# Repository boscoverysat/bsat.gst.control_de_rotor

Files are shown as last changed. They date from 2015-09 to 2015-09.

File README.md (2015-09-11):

# Control de Rotor

## Resumen

Este repositorio contiene la adaptación de la electrónica de control empleada para el rotor de antena basado en el proyecto **[SatNOGS](https://satnogs.org/)**

## Autoría y Licencia

- Autor: **Dailos Rafael Díaz Lara** ( ddialar@gmail.com )
- Fecha: **11/09/2015**
- Versión: **1.0.0**
- Licencia: Creaive Commons 4.0 logo (http://creativecommons.org/licenses/by-nc-sa/4.0/)

## Requisitos previos

- Tener instalado el entorno de desarrollo para Arduino.
- Tener instalado el software Eagle PCB 6.5.0+.

## Procedimiento

Este repositorio contiene la adaptación de la electrónica de control empleada para el rotor de antena basado en el proyecto **[SatNOGS](https://satnogs.org/)** ([Repositorio de origen](https://github.com/satnogs/satnogs-rotator-controller)).

Esta adaptación se ha realizado para utilizar una placa **Ardino Duemilanove** en lugar de la placa *Ardiono Pro Micro*
empleada originalmente.

Para poder llevar a cabo esta adaptación, además de reorganizar la electrónica en torno a los pines del Arduino a emplear,
ha sido necesario reconfigurar los pines dentro del código fuente que será cargado en el microcontrolador.

La organización de directorios de este repositorio es la siguiente:

### [arduino](arduino/)

Contiene el archivo de código fuente que debe cargarse en el microcontrolador.

Para que este script funcione, es necesario incorporar en nuestro entorno de desarrollo, una librería adicional
que no suele venir con la instalación estándar. Dicha librería es **AccelStepper.h** y puede ser localizada
en el siguiente [enlace](https://github.com/adafruit/AccelStepper).

Para concluir, hay que indicar que la única diferencia entre el script original y el empleado en este repositorio, reside en que se ha modificado la numeración de los pines empleados para el control de los motores paso a paso, así como para la detección de la posición HOME de los ejes de Elevación y Azimuth.

En el código fuente que contiene el directorio, se ha mantenido la definición original de pines (comentada para que no tenga efecto en el código), con el propósito que sirva de referencia en futuras investigaciones.

### [img](img/)

Contiene una imagen del conexionado de la placa PCB.

### [pcb](pcb/)

Contiene el proyecto de placa de circuito impreso, realizado con el software **Eagle 6.5.0**.

### [pdf](pdf/)

Contiene el esquema electrónico y el diagrama PCB listos para ser impresos.

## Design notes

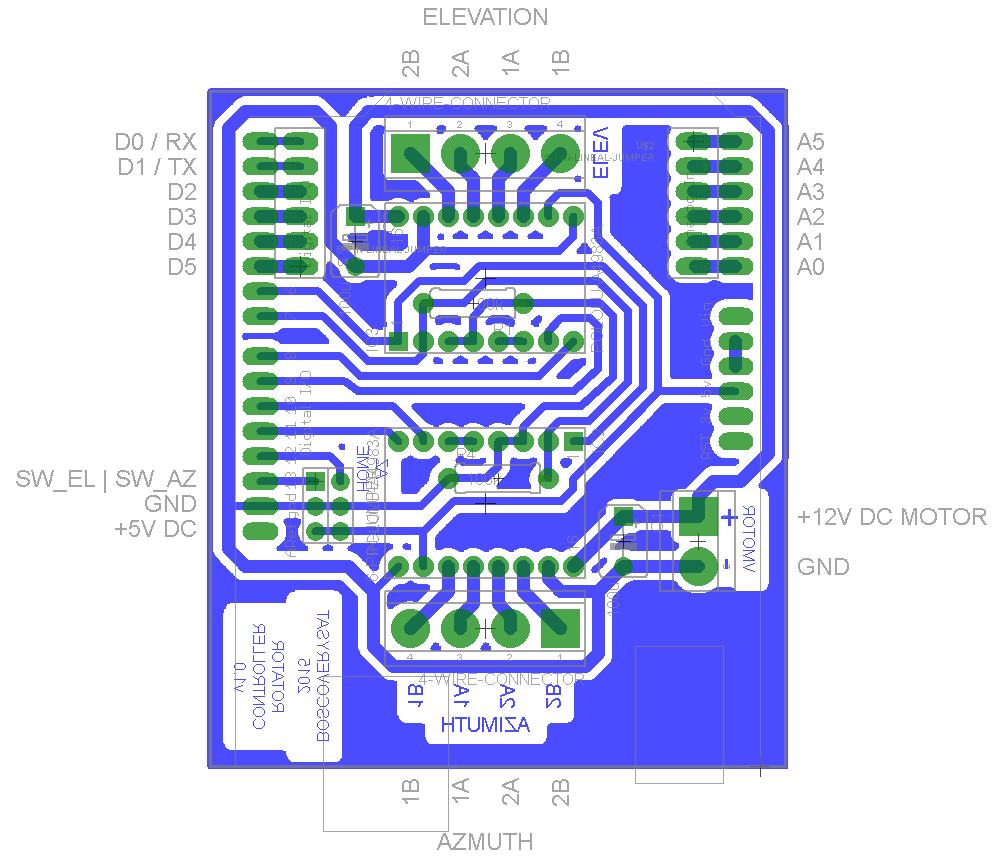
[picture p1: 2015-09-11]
img/Rotator Controller - Arduino Duemilanove.png

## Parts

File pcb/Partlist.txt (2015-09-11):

Partlist

Exported from SatNOGSBoard UNO.brd at 11/09/2015 22:43:30

EAGLE Version 6.5.0 Copyright (c) 1988-2013 CadSoft

Assembly variant: 

Part     Value               Package             Library      Position (inch)       Orientation

C1       100u                B45181B             resistor     (1.85 1.3)            R270
C2       100u                B45181B             resistor     (0.78 2.5)            R270
IC1      ARDUINOUNO          ARDUINO             boscoverysat (2.4 0.4)             R90
IC2      POLOLU-A4983A       POLOLU-A4983        boscoverysat (1.3 1.45)            R270
IC3      POLOLU-A4983A       POLOLU-A4983        boscoverysat (1.3 2.35)            R90
MOTOR_1  4-WIRE-CONNECTOR    4-WIRE-CONNECTOR    boscoverysat (1.3 0.95)            R180
MOTOR_2  4-WIRE-CONNECTOR    4-WIRE-CONNECTOR    boscoverysat (1.3 2.85)            R0
R1       100k                0309/10             resistor     (1.25 2.25)           R180
R4       100k                0309/10             resistor     (1.35 1.55)           R0
SW       6-PIN-JUMPER        6-PIN-JUMPER        boscoverysat (0.62 1.54)           R270
U$1      6-PIN-LINEAL-JUMPER 6-PIN-LINEAR-JUMPER boscoverysat (0.56 2.4)            R0
U$2      6-PIN-LINEAL-JUMPER 6-PIN-LINEAR-JUMPER boscoverysat (2.13 2.9)            R180
VMOTOR   2-WIRE-CONNECTOR    2-WIRE-CONNECTOR    boscoverysat (2.15 1.3)            R270

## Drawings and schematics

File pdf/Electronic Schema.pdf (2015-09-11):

A

A

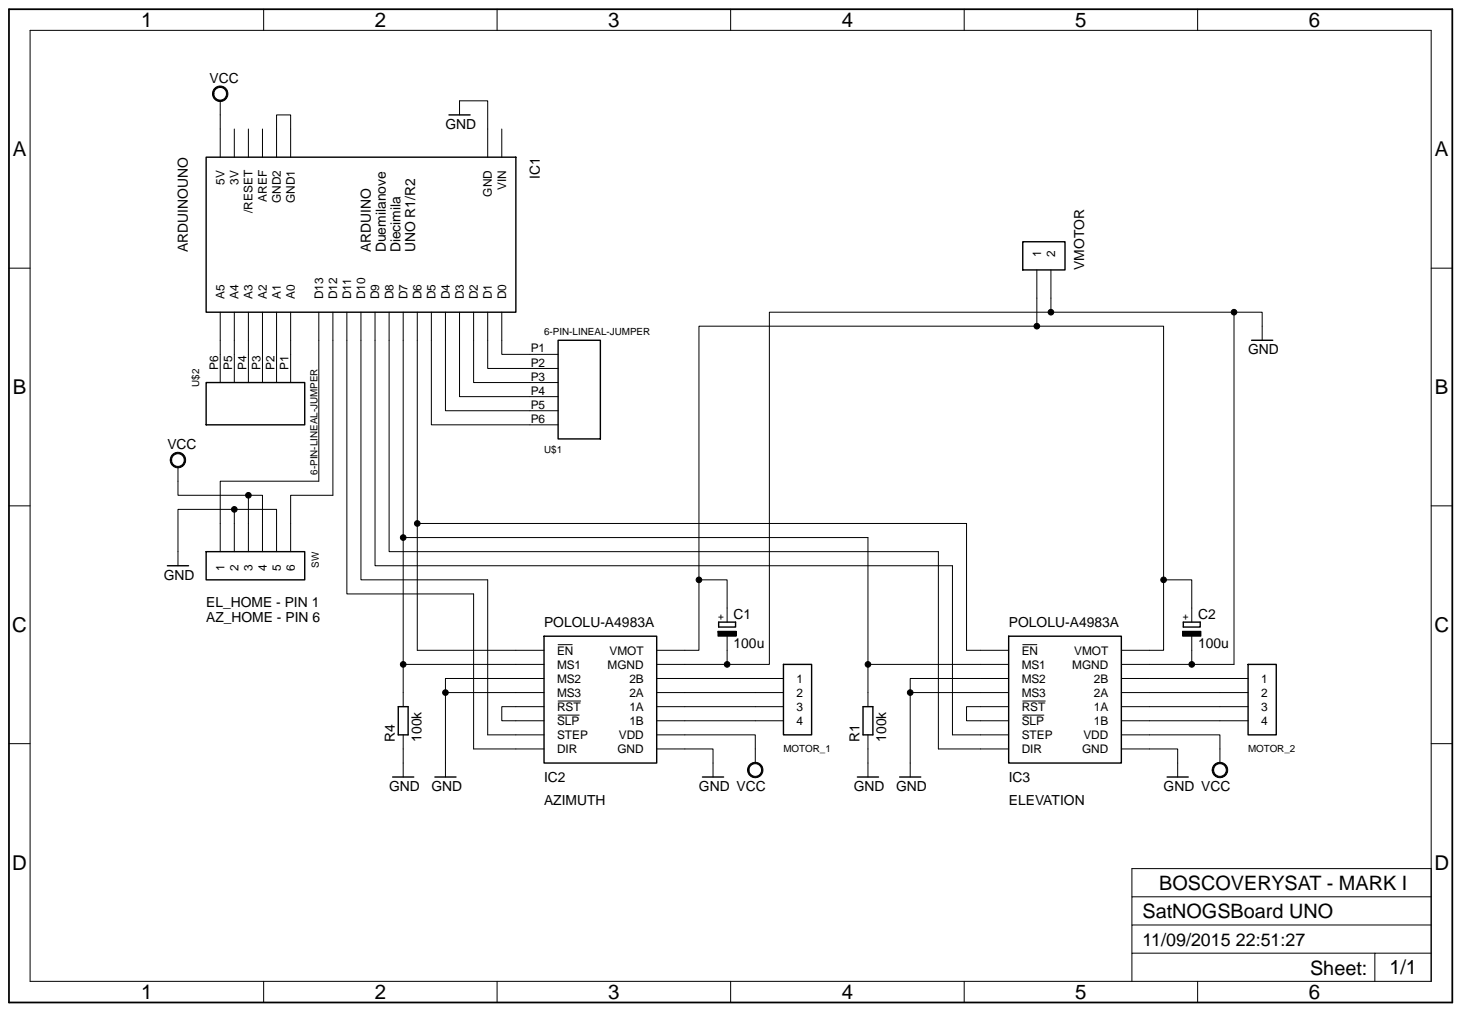
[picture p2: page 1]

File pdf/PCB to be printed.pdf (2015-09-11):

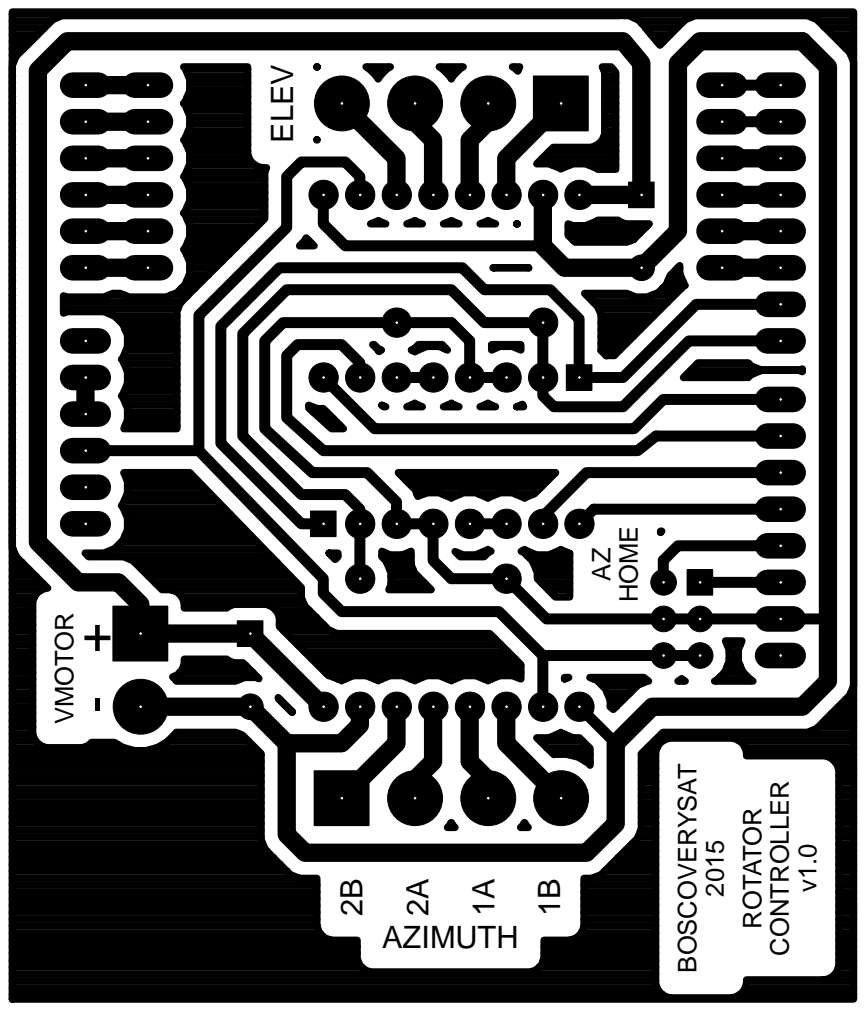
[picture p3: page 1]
ROTATOR; CONTROLLER; BOSCOVERYSAT; VMOTOR; AZIMUTH; HOME; ELEV

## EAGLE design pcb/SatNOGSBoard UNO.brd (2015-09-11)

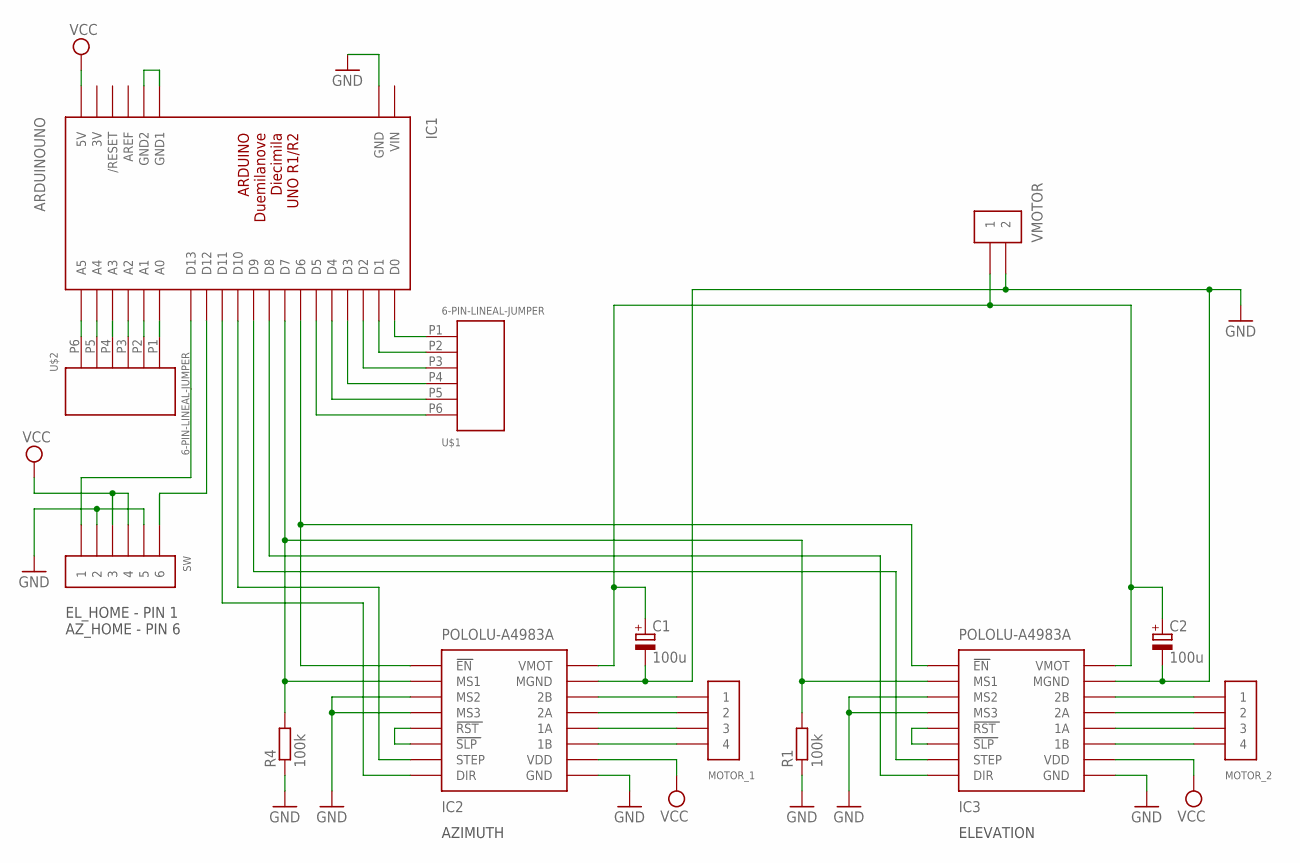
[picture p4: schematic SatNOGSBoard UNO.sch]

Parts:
C1, C2: 100u; B45181B
IC1: ARDUINOUNO; ARDUINO
IC2, IC3: POLOLU-A4983A; POLOLU-A4983
MOTOR_1, MOTOR_2: 4-WIRE-CONNECTOR
R1, R4: 100k; 0309/10
SW: 6-PIN-JUMPER
U$1, U$2: 6-PIN-LINEAL-JUMPER; 6-PIN-LINEAR-JUMPER
VMOTOR: 2-WIRE-CONNECTOR

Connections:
3V: IC1.3V
GND: C1.-, C2.-, IC1.GND, IC2.P$3 (MS2), IC2.P$4 (MS3), IC2.P$9 (GND), IC2.P$15 (MGND), IC3.P$3 (MS2), IC3.P$4 (MS3), IC3.P$9 (GND), IC3.P$15 (MGND), R1.1, R4.1, SW.P$2 (2), SW.P$5 (5), VMOTOR.P$2 (2)
unnamed: IC1.D6, IC2.P$1 (EN), IC3.P$1 (EN)
unnamed: IC1.D7, IC2.P$2 (MS1), IC3.P$2 (MS1), R1.2, R4.2
unnamed: IC3.P$5 (RST), IC3.P$6 (SLP)
unnamed: IC1.D9, IC3.P$7 (STEP)
unnamed: IC1.D8, IC3.P$8 (DIR)
unnamed: IC1.D0, U$1.P1
unnamed: IC1.D1, U$1.P2
unnamed: IC1.D11, IC2.P$8 (DIR)
unnamed: IC1.D12, SW.P$6 (6)
unnamed: IC3.P$14 (2B), MOTOR_2.P$1 (1)
unnamed: IC3.P$13 (2A), MOTOR_2.P$2 (2)
unnamed: IC3.P$12 (1A), MOTOR_2.P$3 (3)
unnamed: IC3.P$11 (1B), MOTOR_2.P$4 (4)
unnamed: IC2.P$5 (RST), IC2.P$6 (SLP)
unnamed: IC1.D2, U$1.P3
unnamed: IC1.D13, SW.P$1 (1)
unnamed: IC1.D3, U$1.P4
unnamed: IC1.D10, IC2.P$7 (STEP)
unnamed: IC2.P$14 (2B), MOTOR_1.P$1 (1)
unnamed: IC2.P$13 (2A), MOTOR_1.P$2 (2)
unnamed: IC2.P$12 (1A), MOTOR_1.P$3 (3)
unnamed: IC2.P$11 (1B), MOTOR_1.P$4 (4)
unnamed: IC1.D4, U$1.P5
unnamed: IC1.D5, U$1.P6
unnamed: IC1.A0, U$2.P1
unnamed: C1.+, C2.+, IC2.P$16 (VMOT), IC3.P$16 (VMOT), VMOTOR.P$1 (1)
unnamed: IC1.A1, U$2.P2
unnamed: IC1.A2, U$2.P3
unnamed: IC1.A3, U$2.P4
unnamed: IC1.A4, U$2.P5
unnamed: IC1.A5, U$2.P6
unnamed: IC1.GND1, IC1.GND2
VCC: IC1.5V, IC2.P$10 (VDD), IC3.P$10 (VDD), SW.P$3 (3), SW.P$4 (4)
VIN: IC1.VIN

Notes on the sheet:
ELEVATION
AZIMUTH
EL_HOME - PIN 1 AZ_HOME - PIN 6

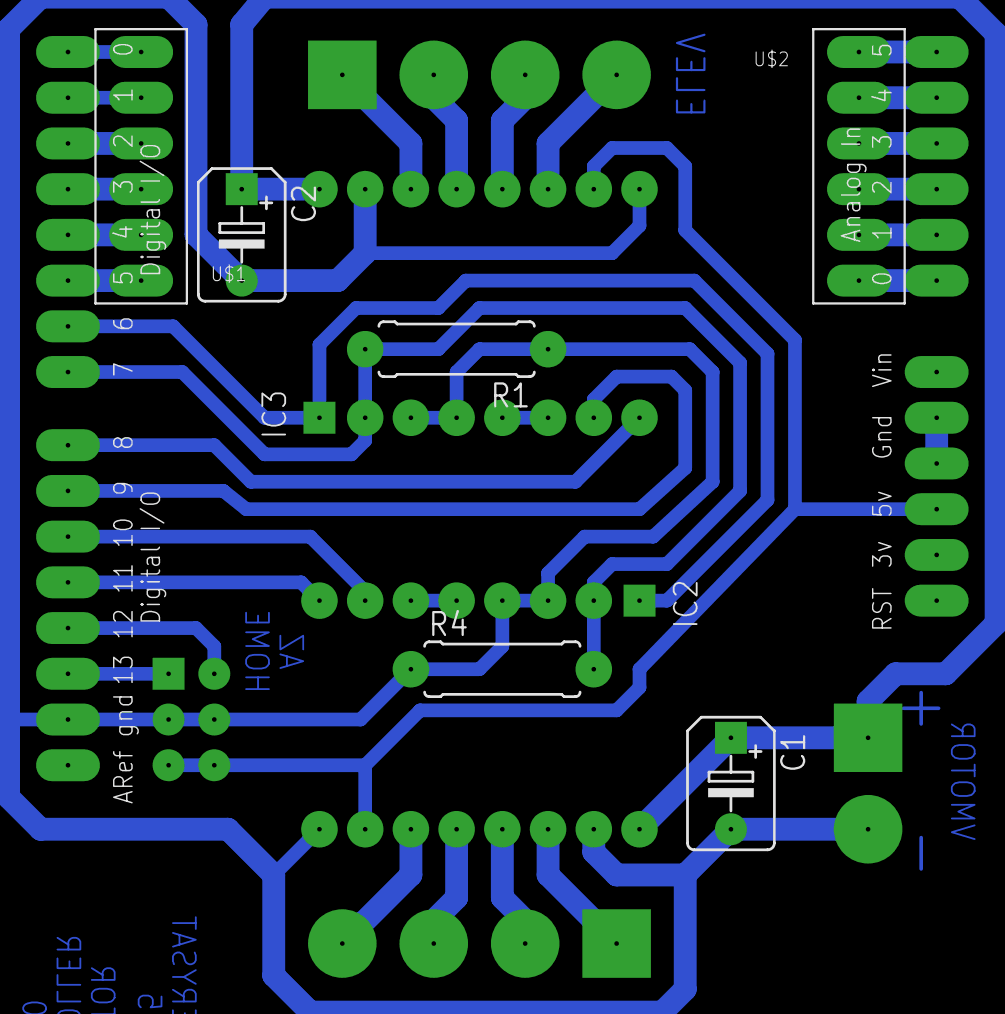
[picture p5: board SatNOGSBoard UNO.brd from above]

Board: 2 copper layers, 13 parts (0 on the bottom side), 34 nets.

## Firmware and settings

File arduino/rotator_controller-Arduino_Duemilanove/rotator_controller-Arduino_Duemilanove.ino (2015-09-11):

#include <string.h>
#include <stdlib.h>
#include <math.h>
#include <AccelStepper.h>

//#define DIR_AZ 18 //PIN for Azimuth Direction
//#define STEP_AZ 10 //PIN for Azimuth Steps
#define DIR_AZ 11 //PIN for Azimuth Direction
#define STEP_AZ 10 //PIN for Azimuth Steps
//#define DIR_EL 6 //PIN for Elevation Direction
//#define STEP_EL 7 //PIN for Elevation Steps
#define DIR_EL 8 //PIN for Elevation Direction
#define STEP_EL 9 //PIN for Elevation Steps

//#define MS1 9 //PIN for step size
//#define EN 8 //PIN for Enable or Disable Stepper Motors
#define MS1 7 //PIN for step size
#define EN 6 //PIN for Enable or Disable Stepper Motors

#define SPR 200 //Step Per Revolution
#define RATIO 60 //Gear ratio
#define T_DELAY 60000 //Time to disable the motors in millisecond

//#define HOME_AZ 4 //Homing switch for Azimuth
//#define HOME_EL 5 //Homing switch for Elevation
#define HOME_AZ 12 //Homing switch for Azimuth
#define HOME_EL 13 //Homing switch for Elevation
/*The MAX_ANGLE depends of ANGLE_SCANNING_MULT and maybe misbehave for large values*/
#define ANGLE_SCANNING_MULT 180 //Angle scanning multiplier
#define MAX_AZ_ANGLE 360 //Maximum Angle of Azimuth for homing scanning
#define MAX_EL_ANGLE 360 //Maximum Angle of Elevation for homing scanning

#define HOME_DELAY 6000 //Time for homing Decceleration in millisecond

/*Global Variables*/
unsigned long t_DIS = 0; //time to disable the Motors
/*Define a stepper and the pins it will use*/
AccelStepper AZstepper(1, STEP_AZ, DIR_AZ);
AccelStepper ELstepper(1, STEP_EL, DIR_EL);

void setup()
{  
  /*Change these to suit your stepper if you want*/
  AZstepper.setMaxSpeed(150);
  AZstepper.setAcceleration(50);
  
  /*Change these to suit your stepper if you want*/
  ELstepper.setMaxSpeed(150);
  ELstepper.setAcceleration(50);
  
  /*Enable Motors*/
  pinMode(EN, OUTPUT);
  digitalWrite(EN, LOW);
  /*Step size*/
  pinMode(MS1, OUTPUT);
  digitalWrite(MS1, LOW); //Full step
  /*Homing switch*/
  pinMode(HOME_AZ, INPUT);
  pinMode(HOME_EL, INPUT);
  /*Serial Communication*/
  Serial.begin(19200);
  /*Initial Homing*/
  Homing(deg2step(-ANGLE_SCANNING_MULT), deg2step(-ANGLE_SCANNING_MULT));
}

void loop()
{ 
  /*Define the steps*/
  static int AZstep = 0;
  static int ELstep = 0;
  /*Time Check*/
  if (t_DIS == 0)
    t_DIS = millis();

  /*Disable Motors*/
  if (AZstep == AZstepper.currentPosition() && ELstep == ELstepper.currentPosition() && millis()-t_DIS > T_DELAY)
  {
    digitalWrite(EN, HIGH);
  }
  /*Enable Motors*/
  else
    digitalWrite(EN, LOW);
    
  /*Read the steps from serial*/
  cmd_proc(AZstep, ELstep);
  /*Move the Azimuth & Elevation Motor*/
  stepper_move(AZstep, ELstep);
}

/*Homing Function*/
void Homing(int AZsteps, int ELsteps)
{
  int value_Home_AZ = HIGH;
  int value_Home_EL = HIGH;
  int n_AZ = 1; //Times that AZ angle has changed
  int n_EL = 1; //Times that EL angle has changed
  boolean isHome_AZ = false;
  boolean isHome_EL = false;
  
  AZstepper.moveTo(AZsteps);
  ELstepper.moveTo(ELsteps);
  
  while(isHome_AZ == false || isHome_EL == false)
  {
    value_Home_AZ = digitalRead(HOME_AZ);
    value_Home_EL = digitalRead(HOME_EL);
    /* Change to LOW according to Home sensor */
    if (value_Home_AZ == HIGH)
    {
      AZstepper.moveTo(AZstepper.currentPosition());
      isHome_AZ = true;
    }   
    /* Change to LOW according to Home sensor */
    if (value_Home_EL == HIGH)
    {
      ELstepper.moveTo(ELstepper.currentPosition());
      isHome_EL = true;
    }
    if (AZstepper.distanceToGo() == 0 && !isHome_AZ)
    {
      n_AZ++;
      AZsteps = deg2step(pow(-1,n_AZ)*n_AZ*ANGLE_SCANNING_MULT);
      if (abs(n_AZ*ANGLE_SCANNING_MULT) > MAX_AZ_ANGLE)
      {
        error(0);
        break;
      }
      AZstepper.moveTo(AZsteps);
    } 
    if (ELstepper.distanceToGo() == 0 && !isHome_EL)
    { 
      n_EL++;
      ELsteps = deg2step(pow(-1,n_EL)*n_EL*ANGLE_SCANNING_MULT);
      if (abs(n_EL*ANGLE_SCANNING_MULT) > MAX_EL_ANGLE)
      {
        error(1);
        break;
      }
      ELstepper.moveTo(ELsteps);
    }
    
    AZstepper.run();
    ELstepper.run();
  }
  /*Delay to Deccelerate*/
  long time = millis();  
  while(millis() - time < HOME_DELAY)
  {  
    AZstepper.run();
    ELstepper.run();
  }
  /*Reset the steps*/
  AZstepper.setCurrentPosition(0);
  ELstepper.setCurrentPosition(0); 
}
 
/*EasyComm 2 Protocol & Calculate the steps*/
void cmd_proc(int &stepAz, int &stepEl)
{
  /*Serial*/
  char buffer[256];
  char incomingByte;
  char *p=buffer;
  char *str;
  static int counter=0;
  char data[100];
  
  double angleAz,angleEl;
  
  /*Read from serial*/
  while (Serial.available() > 0)
  {
    incomingByte = Serial.read();
    /* XXX: Get position using custom and test code */
    if (incomingByte == '!')
    {
      /* Get position */
      Serial.print("TM");
      Serial.print(1);
      Serial.print(" ");
      Serial.print("AZ");
      Serial.print(10*step2deg(AZstepper.currentPosition()), 1);
      Serial.print(" ");
      Serial.print("EL");
      Serial.println(10*step2deg(ELstepper.currentPosition()), 1);
    }
    /*new data*/
    else if (incomingByte == '\n')
    {
      p = buffer;
      buffer[counter] = 0;
      if (buffer[0] == 'A' && buffer[1] == 'Z')
      {
        if (buffer[2] == ' ' && buffer[3] == 'E' && buffer[4] == 'L')
        {
          /* Get position */
          Serial.print("AZ");
          Serial.print(step2deg(AZstepper.currentPosition()), 1);
          Serial.print(" ");
          Serial.print("EL");
          Serial.print(step2deg(ELstepper.currentPosition()), 1);
          Serial.println(" ");
        }
        else
        {
          /*Get the absolute value of angle*/
          str = strtok_r(p, " " , &p);
          strncpy(data, str+2, 10);
          angleAz = atof(data);
          /*Calculate the steps*/
          stepAz = deg2step(angleAz);

          /*Get the absolute value of angle*/
          str = strtok_r(p, " " , &p);
          if (str[0] == 'E' && str[1] == 'L')
          {
            strncpy(data, str+2, 10);
            angleEl = atof(data);
            /*Calculate the steps*/
            stepEl = deg2step(angleEl);
          }
        }
      }
      /* Stop Moving */
      else if (buffer[0] == 'S' && buffer[1] == 'A' && buffer[2] == ' ' && buffer[3] == 'S' && buffer[4] == 'E')
      {
        /* Get position */
        Serial.print("AZ");
        Serial.print(step2deg(AZstepper.currentPosition()), 1);
        Serial.print(" ");
        Serial.print("EL");
        Serial.println(step2deg(ELstepper.currentPosition()), 1);
        stepAz = AZstepper.currentPosition();
        stepEl = ELstepper.currentPosition();
      }
      /* Reset the rotator */
      else if (buffer[0] == 'R' && buffer[1] == 'E' && buffer[2] == 'S' && buffer[3] == 'E' && buffer[4] == 'T')
      {
        /* Get position */
        Serial.print("AZ");
        Serial.print(step2deg(AZstepper.currentPosition()), 1);
        Serial.print(" ");
        Serial.print("EL");
        Serial.println(step2deg(ELstepper.currentPosition()), 1);
        /*Move the steppers to initial position*/
        Homing(0,0);
        /*Zero the steps*/
        stepAz = 0;
        stepEl = 0;
      }      
      counter = 0;
      /*Reset the disable motor time*/
      t_DIS = 0;
    }
    /*Fill the buffer with incoming data*/
    else {
      buffer[counter] = incomingByte;
      counter++;
    }
  }
}

/*Error Handling*/
void error(int num_error)
{
  switch (num_error)
  {
    /*Azimuth error*/
    case (0):
      while(1)
      {
        Serial.println("AL001");
        delay(100);
      }
    /*Elevation error*/
    case (1):
      while(1)
      {
        Serial.println("AL002");
        delay(100);
      }
    default:
      while(1)
      {
        Serial.println("AL000");
        delay(100);
      }
  }
}

/*Send pulses to stepper motor drivers*/
void stepper_move(int stepAz, int stepEl)
{
  AZstepper.moveTo(stepAz);
  ELstepper.moveTo(stepEl);
    
  AZstepper.run();
  ELstepper.run();
}

/*Convert degrees to steps*/
int deg2step(double deg)
{
  return(RATIO*SPR*deg/360);
}

/*Convert steps to degrees*/
double step2deg(int Step)
{
  return(360.00*Step/(SPR*RATIO));
}

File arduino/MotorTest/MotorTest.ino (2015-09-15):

/*
  Motor Test.
  Author: @goyoregalado
  
*/
 
const char FWD = 'W';
const char BCK = 'S';
const int HALFDUTY = 127;

const int directionPin = 13;
const int enablePin = 12;
const int stepPin = 11;
const int stepConfPin = 10;

void setup() {
  Serial.begin(9600);
  pinMode(directionPin, OUTPUT);
  pinMode(enablePin, OUTPUT);
  pinMode(stepPin, OUTPUT);
  pinMode(stepConfPin, OUTPUT);
  
  digitalWrite(enablePin, LOW);
  digitalWrite(directionPin, HIGH);
  digitalWrite(stepConfPin, LOW);
  
  Serial.println("You can interact with the controller using these keys: ");
  Serial.println("W-> Move forward");
  Serial.println("S-> Move backwards");
}

// the loop routine runs over and over again forever:
void loop() {
  if (Serial.available() > 0) {
    char c = Serial.read();
    if (c == FWD) {
      Serial.println("Moving forward");
      digitalWrite(directionPin, HIGH);
    }
    else if (c == BCK) {
      Serial.println("Moving backward");
      digitalWrite(directionPin, LOW);
    }
  }
  analogWrite(stepPin, HALFDUTY);
  delay(100);
}

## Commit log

2015-09-12 Añadido diseño de PCB y script de control para Arduino Duemilanove.
    [SatNOGSBoard UNO.brd, SatNOGSBoard UNO.sch]
2015-09-15 Añadido sketch para la comprobación del funcionamiento de los pololus
